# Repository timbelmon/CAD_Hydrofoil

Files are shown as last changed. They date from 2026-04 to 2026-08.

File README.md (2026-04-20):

# CAD Hydrofoil

Semester project focused on developing a self-stabilizing RC hydrofoil.

The system uses a T-foil design with custom PCB-based water sensors acting as the control “legs” to detect water contact and stabilize the craft in real time.

Core components:
- Custom-designed hydrofoil (CAD)
- Self-manufactured PCBs (water sensing + control)
- Arduino-based control system

The goal is to create a fully integrated, self-stabilizing hydrofoil platform combining mechanical design, electronics, and embedded control.

## Basic Sketch
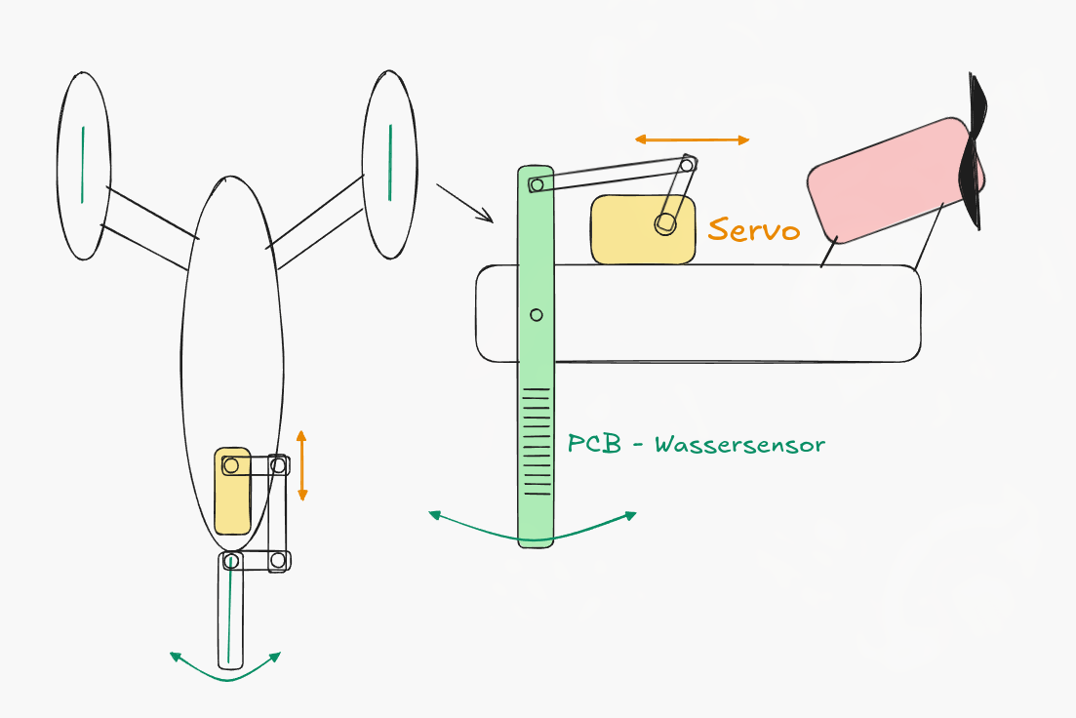
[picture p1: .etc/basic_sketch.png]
sketch


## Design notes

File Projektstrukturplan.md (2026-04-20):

---

kanban-plugin: board

---

## Planung

- [x] 110 Finales Konzept entscheiden
- [x] 120 Kanbanplan
- [x] 130 Meilensteinplan
- [x] 140 GANTT Diagramm
- [ ] 150 Networking FabLab

## Grundfunktionen

- [x] 210 Antriebe Testen
- [ ] 220 Schematic Schiff
- [ ] 230 Code Schiff
- [ ] 240 Schematic Remote
- [ ] 250 Code Remote
- [ ] 260 Schematics Testen

## Prototyp

- [ ] 310 Auftriebs- & Gewichtskalkulation
- [ ] 320 NACA-Profil fürs Foil?
- [ ] 330 Foil-Konstruktion
- [ ] 340 PCB Schiff
- [ ] 350 PCB Remote
- [ ] 360 PCB & Schematic Foils
- [ ] 370 Platinen Löten
- [ ] 380 Code Foil Movement
- [ ] 390 Failsafe-Programmierung (Funk-Abbruch)

## Final Assembly

- [ ] 410 FreeCad SHIP SIM?
- [ ] 420 Rumpf-Design
- [ ] 425 CAD Remote
- [ ] 430 Final Assembly
- [ ] 440 Abdichtung (Waterproofing)

## Abschluss

- [ ] 510 Plakat Design
- [ ] 520 Projektbericht und Reflexion

%% kanban:settings
```
{"kanban-plugin":"board","list-collapse":[false,false,false,false,false,false,false,false,false,false,false,false]}
```
%%

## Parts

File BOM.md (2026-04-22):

- 3xArduino Nano
- 2xHochleistungsmotor 4,5V DC - 3,4 W, d=24,2mm, L=30,5mm
- 1xMotortreiber - L298N 2V-10V 1,5 A 2-Kanal PWM
- 2xPropeller
- 3x18650 Akku
- 3xSG92R Micro Servo Motor
- 2xFunkmodul - NRF24L01
- 1xStep-Down Modul AMS1117 3,3 V
- 1xJoystick 2 Achsen
- 6xBatterieklemmen

Fehlt:
- 6xBuchsenleiste / Header Pin Female - 1 x 15P - 2.54mm
	- https://arduino-projekte.info/products/buchsenleiste-header-pin-female-1-x-15p-2-54mm
- 1xXT30 Kabel (Durschneiden)
	- https://www.monsterhopups.de/GForce-GF-1311-010-Power-Verlaengerungskabel-XT-30-14Awg-Silikon-Kabel-12Cm-1-St

Nice to have:
- 1xSchiebepoti
	- https://botland.de/schwerkraft-encoder-und-potentiometer/11258-dfrobot-gravity-54k-schiebepotentiometer-6959420901036.html

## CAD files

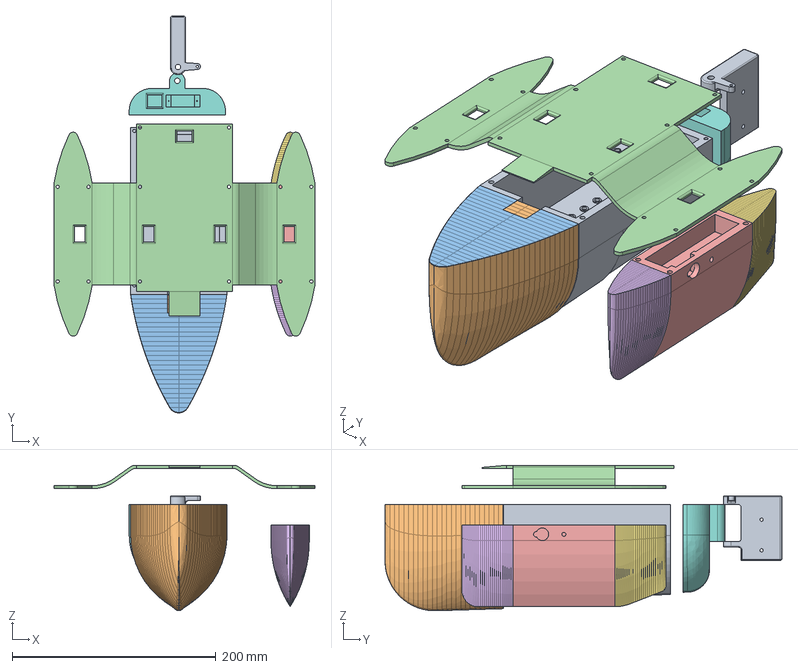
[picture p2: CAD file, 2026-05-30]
FreeCAD_Schiff/Trimaran-Hydrofoil.FCStd
256.0 x 389.3 x 142.7 mm
PCBBody
Front Part
Träger
CurvedArray
CurvedArray002
Back
Körper001

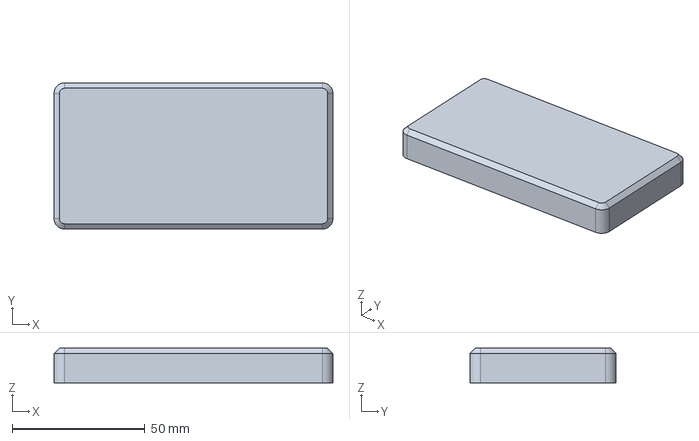
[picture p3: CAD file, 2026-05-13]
FreeCAD_Remote/Hydrofoil_Controller_Bottom.FCStd
105.0 x 55.0 x 13.0 mm

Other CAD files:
FreeCAD_Remote/Hydrofoil_Controller.FCStd

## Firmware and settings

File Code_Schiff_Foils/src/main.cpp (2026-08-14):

#include <Arduino.h>
#include <Servo.h>

// --- Pin Definitions ---
const int ANALOG_PIN_1 = A2;  // Pin 21 (Resistor 1)
const int ANALOG_PIN_2 = A1;  // Pin 20 (Resistor 2)
const int SERVO_PIN_1  = 2;   // Pin 5  (D2)
const int SERVO_PIN_2  = 3;   // Pin 6  (D3)

// --- Hardware Constants ---
const float R_REF = 100000.0;  // Value of your reference resistors to GND (100k Ohms)

// --- PID Tuning Parameters ---
const float Kp = 0.1;  // Proportional gain
const float Ki = 0.05; // Integral gain
const float Kd = 0.01; // Derivative gain

// --- PID Target / Setpoint ---
const float SETPOINT = 95000.0; 

// --- Servo Objects ---
Servo servo1;
Servo servo2;

// --- PID State Variables ---
struct PIDState {
    float integral = 0.0;
    float lastError = 0.0;
};

PIDState pid1;
PIDState pid2;

unsigned long lastTime = 0;

// --- Function Declarations ---
float readResistance(int pin);
float updatePID(float currentInput, PIDState &state, float dt);
    
void setup() {
    Serial.begin(115200);
    
    servo1.attach(SERVO_PIN_1);
    servo2.attach(SERVO_PIN_2);
    
    // Initialize servos to center position (90 degrees)
    servo1.write(90);
    servo2.write(90);
    
    lastTime = millis();
}

void loop() {
    // unsigned long currentTime = millis();
    // float dt = (currentTime - lastTime) / 1000.0; // Delta time in seconds
    
    // // Fallback for timing anomalies or initial loops
    // if (dt <= 0.0) dt = 0.01; 
    // lastTime = currentTime;

    // // 1. Measure actual resistances
    // float r1 = readResistance(ANALOG_PIN_1);
    // float r2 = readResistance(ANALOG_PIN_2);

    // // 2. Compute PID outputs
    // float output1 = updatePID(r1, pid1, dt);
    // float output2 = updatePID(r2, pid2, dt);

    // // 3. Map PID output to Servo degrees (60 to 120)
    // // Limits the physical movement to 30 degrees maximum in either direction from 90
    // int servoPos1 = constrain(90 + (int)output1, 60, 120);
    // int servoPos2 = constrain(90 + (int)output2, 60, 120);

    // // 4. Actuate Servos
    // servo1.write(servoPos1);
    // servo2.write(servoPos2);

    // // Debugging output over Serial Monitor
    // Serial.print("R1: "); Serial.print(r1);
    // Serial.print(" -> S1: "); Serial.print(servoPos1);
    // Serial.print(" | R2: "); Serial.print(r2);
    // Serial.print(" -> S2: "); Serial.println(servoPos2);

    // delay(20); // Small delay to decouple loop speed and prevent serial spam
}

/**
 * Calculates the resistance of the upper resistor in the voltage divider.
 */
float readResistance(int pin) {
    int adcVal = analogRead(pin);
    
    // Handle edge cases to avoid division by zero or negative calculation bounds
    if (adcVal >= 1023) return 0.0; 
    if (adcVal <= 0) return 999999.0; 

    // Voltage divider calculation
    float resistance = R_REF * ((1023.0 / (float)adcVal) - 1.0);
    return resistance;
}

/**
 * Standard positional PID algorithm loop.
 */
float updatePID(float currentInput, PIDState &state, float dt) {
    // Calculate Error
    float error = SETPOINT - currentInput;

    // Proportional term
    float Pout = Kp * error;

    // Integral term
    state.integral += error * dt;
    float Iout = Ki * state.integral;

    // Derivative term
    float derivative = (error - state.lastError) / dt;
    float Dout = Kd * derivative;

    // Save current error for the next iteration step
    state.lastError = error;

    // Combined output
    float output = Pout + Iout + Dout;

    // Anti-windup clamping limited to +/- 30 degrees
    if (output > 30.0) {
        output = 30.0;
        state.integral -= error * dt; 
    } else if (output < -30.0) {
        output = -30.0;
        state.integral -= error * dt;
    }

    return output;
}

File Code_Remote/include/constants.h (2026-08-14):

#pragma once
#include <stdint.h>

namespace constantsCom
{
    const uint8_t bufferSize = 32;
    const uint8_t steerMin = 64;
    const uint8_t steerMax = 127;
    const bool throttleToggle = false;
    const uint8_t throttleMin = 129;
    const uint8_t throttleMax = 255;
    const uint8_t throttleOn = 2;
    const uint8_t throttleOff = 3;
    const uint8_t throttleRev = 4;
    const uint8_t foilToggle = 5;
}

namespace constantsPinsShip
{
    const uint8_t foilPin = 10;
    const uint8_t servoSteerPin = 2;
    const uint8_t csnPin = 8;
    const uint8_t cePin = 7;
    const uint8_t in1Pin = 3;
    const uint8_t in2Pin = 5;
    const uint8_t in3Pin = 6;
    const uint8_t in4Pin = 5;
}

namespace constantsShip
{
    const uint8_t steerAngleMax = 90;
    const uint8_t steerMidpoint = 90;
}

namespace constantsPinsRemote
{
    const uint8_t cePin = 7;
    const uint8_t csnPin = 8;
    const uint8_t foilPin = 2;
    const uint8_t speedPin = A0;
    const uint8_t joyXPin = A1;
}

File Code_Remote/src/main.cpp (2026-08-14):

/*
 * Arduino Wireless Communication Tutorial
 * Example 1 - Transmitter Code
 *
 * by Dejan Nedelkovski, www.HowToMechatronics.com
 *
 * Library: TMRh20/RF24, https://github.com/tmrh20/RF24/
 */

#include <Arduino.h>
#include <printf.h>
#include <SPI.h>
#include <nRF24L01.h>
#include <RF24.h>
#include <constants.h>

#define THRESHOLD 10 // change if needed

// Radio module setup
//RF24 radio(constantsPinsRemote::cePin, constantsPinsRemote::csnPin);
// Explicitly type your physical pins here (e.g., 7 and 8)
RF24 radio(7, 8);

const byte address[6] = "00005";

// Buffer for sending data
uint8_t buffer[constantsCom::bufferSize];

// Pins
const int joyX = constantsPinsRemote::joyXPin;
const int speedPin = constantsPinsRemote::speedPin;
const int foilPin = constantsPinsRemote::foilPin;

// safe data for sending
int lastX = 0;
int lastSpeed = 0;
bool lastbutton = false;

// --- DEBUGGING VARIABLES ---
unsigned long lastLogTime = 0;
const unsigned long logInterval = 250; // Print debug info every 250ms

void setup()
{
  pinMode(foilPin, INPUT_PULLUP);
  // 1. IMMEDIATELY turn the LED on so we know the Nano is running
  pinMode(LED_BUILTIN, OUTPUT);
  digitalWrite(LED_BUILTIN, HIGH); 
  Serial.begin(9600);
  printf_begin();

  Serial.println("Booting up... testing radio next.");
  delay(500); // Give you a moment to see it solid ON

  // 2. Now try the radio. If it freezes here, the LED will stay SOLID ON.
  if (!radio.begin())
  {
    Serial.println("Hardware not responding! Check your wiring.");
    radio.printDetails();
    
    // If it fails but doesn't freeze, it will start blinking
    SPI.end();
    while (true)
    {
      digitalWrite(LED_BUILTIN, HIGH);
      delay(100);
      digitalWrite(LED_BUILTIN, LOW);
      delay(100);
    }
  }

  radio.openWritingPipe(address);
  radio.setPALevel(RF24_PA_MAX);
  radio.stopListening();
  
  Serial.println("Remote Initialized successfully!");
  
}

void loop()
{
  // Clear buffer if needed
  memset(buffer, 0, constantsCom::bufferSize);

  int i = 0;

  // Keep Alive start byte
  buffer[i++] = 1;

  // Steering
  int x = analogRead(joyX);
  uint8_t steer = 0; // Temp variable to store mapped value for debugging

  // Send data when the change is significant
  if (abs(x - lastX) > THRESHOLD)
  {
    // TODO: THIS VALUE NEEDS CALEBRATION WHEN THE PCB IS READY
    int maxReadSteer = 1023;
    steer = map(x, 0, maxReadSteer,
                    constantsCom::steerMin,
                    constantsCom::steerMax);
    buffer[i++] = steer;
    lastX = x;
  }
  else 
  {
    // If not updated this frame, calculate what it currently sits at for debug visibility
    steer = map(x, 0, 1023, constantsCom::steerMin, constantsCom::steerMax);
  }

// Motor speed / Throttle
  int speed = analogRead(speedPin);
  uint8_t mappedSpeed = 0; 

  // 1. Update maxRead to 680 based on your actual hardware ceiling
  int maxRead = 680;
  int potMiddle = 500;
  int constrainedSpeed = constrain(speed, 0, maxRead);

  // Calculate the target middle value for your radio throttle
  int throttleMid = (constantsCom::throttleMin + constantsCom::throttleMax) / 2;

  // 2. Check threshold against the constrained value
  if (abs(constrainedSpeed - lastSpeed) > THRESHOLD)
  {
    lastSpeed = constrainedSpeed;
    
    // 3. Piece-wise mapping to linearize the logarithmic pot
    if (constrainedSpeed <= potMiddle)
    {
      // Map the aggressive lower half of the pot (0 to 500)
      speed = map(constrainedSpeed, 0, potMiddle, constantsCom::throttleMax, throttleMid);
    }
    else
    {
      // Map the flatter upper half of the pot (500 to 680)
      speed = map(constrainedSpeed, potMiddle, maxRead, throttleMid, constantsCom::throttleMin);
    }
    
    buffer[i++] = speed;
    mappedSpeed = speed;
  }
  else
  {
    // If not updated this frame, calculate for debug visibility
    if (constrainedSpeed <= potMiddle)
    {
      mappedSpeed = map(constrainedSpeed, 0, potMiddle, constantsCom::throttleMax, throttleMid);
    }
    else
    {
      mappedSpeed = map(constrainedSpeed, potMiddle, maxRead, throttleMid, constantsCom::throttleMin);
    }
  }

 // Motor button
  // Standard INPUT_PULLUP logic: 
  // LOW means the button is physically making contact with Ground (PRESSED)
  // HIGH means the internal resistor is pulling it up (RELEASED)
  int pinReading = digitalRead(foilPin);
  bool button = (pinReading == LOW); 

  // Only trigger the event on the transition from RELEASED to PRESSED
  if (button && !lastbutton)
  {
    buffer[i++] = constantsCom::foilToggle;
    Serial.println("--- BUTTON TOGGLE EVENT TRIGGERED ---"); // Temporary action alert
  }
  
  // Update your tracking state so it doesn't continuously trigger
  lastbutton = button;

  // --- SERIAL DEBUGGING OUTPUT ---
  if (millis() - lastLogTime >= logInterval)
  {
    lastLogTime = millis();
    
    Serial.print("--- DEBUG DATA ---");
    Serial.print(" | Joystick X (Raw): ");  Serial.print(x);
    Serial.print(" -> Mapped: ");           Serial.print(steer);
    
    Serial.print(" | Throttle (Raw): ");    Serial.print(analogRead(speedPin)); // Fresh raw read
    Serial.print(" -> Mapped: ");           Serial.print(mappedSpeed);
    
    Serial.print(" | Button: ");           Serial.println(button ? "PRESSED" : "RELEASED");
  }

  // Send
  radio.write(buffer, constantsCom::bufferSize);

  delay(20);
}

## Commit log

2026-04-20 KiCad Boot hinzugefügt
    [Schiff.kicad_pcb, Schiff.kicad_sch]
2026-04-20 Initialize README with project details
    Added project overview and core components for CAD Hydrofoil.
2026-04-20 (Test)Code NRF-Modul
    Test Code zum empfangen von Daten mit dem NRF-Modul (funktioniert)
    Und aktualisierter Footprint der Arduinos in KiCad
    [Schiff.kicad_pcb, Schiff.kicad_sch]
2026-04-21 Neuer Ordner (Code_Remote)
    Es wurde ein neuer Ordner für Code_Remote erstellt, aktuell ist der Code ein Dummy Code, der "Hello World" sendet
2026-04-23 Added basic Remote Shell
    [Hydrofoil_Controller.FCStd, Hydrofoil_Controller_Bottom.FCStd]
2026-04-27 changed Pinout on Arduino in KiCad
    The pinout in schematic was changed to match the code
    [Schiff.kicad_sch]
2026-05-05 New footprints for parts
    [Schiff.kicad_pcb, Schiff.kicad_sch]
2026-05-06 Begining of the layout
    Unfinished layout of the Hydrofoil
    [Schiff.kicad_pcb]
2026-05-06 Some little changes to schematic
    One new connection on schematic
    [Schiff.kicad_sch]
2026-05-06 Save for new test-Branch (PCB)
2026-05-06 Changed footprints
    Changed footprints to match the given bore sizes
    [Schiff.kicad_pcb, Schiff.kicad_sch]
2026-05-06 New layout for hydrofoil
    This layout needs to be checked, a specially in terms of ground connections and the width of these connections
    [Schiff.kicad_pcb, Schiff.kicad_sch]
2026-05-08 New optimized PCB for foil
    New PCB, with seemingly working ground-plane (the ground-plane still needs thorough review)
    [Schiff.kicad_pcb, Schiff.kicad_sch]
2026-05-08 final PCB with mounting holes
    [Schiff.kicad_pcb, Schiff.kicad_sch]
2026-05-09 small changes to the PCB
    New bridge on ground-plane and moved some traces for better and bigger connections on the ground-plane
    [Schiff.kicad_pcb]
2026-05-13 CAD-Design Hydrofoil Body (Outer Stabilizer)
    Added parametric Outer Stabilizer
    [OuterStabilizer.FCStd]
2026-05-13 Renamed Folders to Match Structure
    [Hydrofoil_Controller.FCStd, Hydrofoil_Controller_Bottom.FCStd, OuterStabilizer.FCStd]
2026-05-20 Added plane on front
    Added plane on front and put it on ground, to reduce machining
    [Schiff.kicad_pcb]
2026-05-20 Batterypack for hydrofoil
    [KiCad_Batterypack.kicad_pcb, KiCad_Batterypack.kicad_sch]
2026-05-20 Added plane
    Added grounded plane on front and back to reduce machining
    [KiCad_Batterypack.kicad_pcb]
2026-05-26 Updated CAD-Design (Outer stabilizer)
    [OuterStabilizer.FCStd]
2026-05-26 New remote
    New remote on a stable KiCad version
    [Remote.kicad_pcb, Remote.kicad_sch]
2026-05-26 Finished Remote
    Remote is finished and need review
    [Remote.kicad_pcb, Remote.kicad_sch]
2026-05-26 Changed tracewidth
    New tracewidth for voltage, because of thinner copper layer
    [Schiff.kicad_pcb]
2026-05-26 Foils for depth measurement
    [Foils.kicad_pcb, Foils.kicad_sch]
2026-05-27 Updated modular CAD-Design for Outer Stabilizer
    [OuterStabilizer.FCStd]
2026-05-27 Changed nettie footprint
    [Remote.kicad_pcb]
2026-05-27 New nettie footprint
    [Schiff.kicad_pcb]
2026-05-27 Updated CAD-Model Trimaran
    [OuterStabilizer.FCStd]
2026-05-27 Rebuild throttle logic
2026-05-29 Updated CAD-Design
    [OuterStabilizer.FCStd]
2026-05-29 Updated Trimaran-Hydrofoil CAD-Design
    [Trimaran-Hydrofoil.FCStd]
2026-05-29 changed foil design to be more suitable for 3d printing
    [Trimaran-Hydrofoil.FCStd]
2026-05-30 made parts stronger and fixed dimension
    [Trimaran-Hydrofoil.FCStd]
2026-05-30 changed folder name to align with repo
    [Trimaran-Hydrofoil.FCStd]
2026-05-30 bugfix steering assembly
    fixed bug from previous improvement
    [Trimaran-Hydrofoil.FCStd]
2026-05-31 New foils
    New foils for better resistance measurement
    [Foils.kicad_pcb]
